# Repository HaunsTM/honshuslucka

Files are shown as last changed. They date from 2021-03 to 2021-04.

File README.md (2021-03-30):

# Chicken house hatch

## Introduction
Chicken house hatch is an example of adapted IoT. It all started as an expressed need of automation for the hatch of a chicken house. In the particular area, roosters weren't allowed to make their morning sounds before 8 A.M. The most peaceful solution was to be able to open/close the hatch remotely via a home automation system, Home Assistant.

This  setup is constituted of

* a PLC (ESP8266/D1 mini with wifi)
* a 12 volt DC / 2 ampere linear actuator
* a 2 relay module
* 2 switch buttons
* a hatch for closing/opening the entrance, constructed as a guillotine

Software

The managing software is developeped as a standard Arduino application and written in C++. Architecturally, it is set up as a state machine. For remote controlling puposes, there is a REST-API as well. State changes are reported as MQTT messages.

## Communication
The actuator can be controlled via either direct switches or remotely via http endpoints.

### Devive info
	example: [link](http://10.0.0.71/info)
	
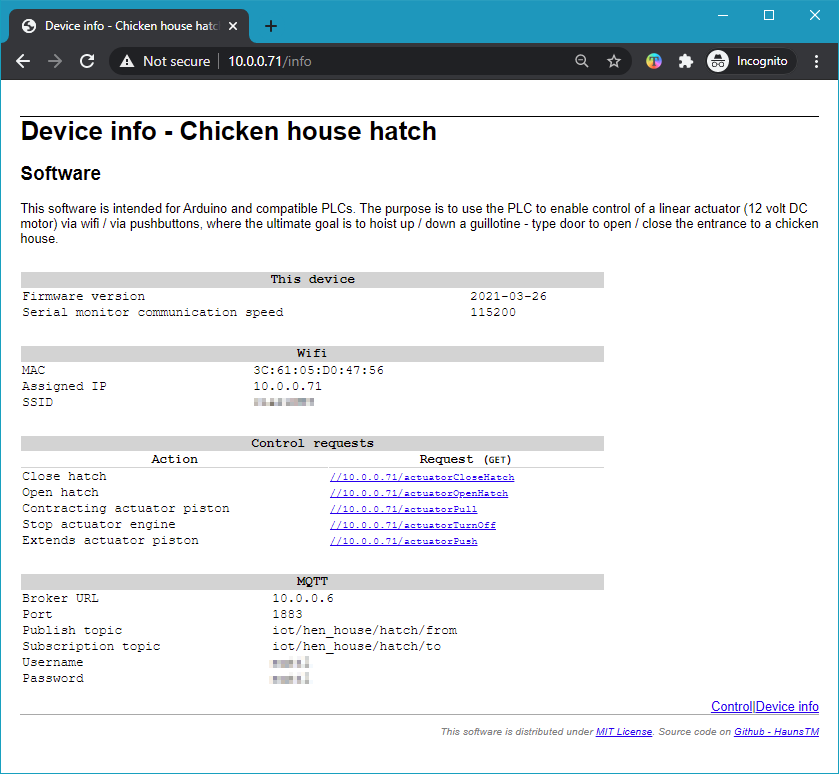
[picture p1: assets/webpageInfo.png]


### Controlling

_server.on("/", [this]() { routeGetControl(); });
<table>
    <thead>
        <tr><td>Action</td><td>Request (GET)</td></tr>
    </thead>
    <tbody>
        <tr><td>Close hatch</td><td>//10.0.0.71/actuatorCloseHatch</td></tr>
        <tr><td>Open hatch</td><td>//10.0.0.71/actuatorOpenHatch</td></tr>
    </tbody>
</table>

<table>
    <thead>
        <tr><td>Action</td><td>Request (GET)</td></tr>
    </thead>
    <tbody>
        <tr><td>Contracting actuator piston</td><td>//10.0.0.71/actuatorPull</td></tr>
        <tr><td>Stop actuator engine</td><td>//10.0.0.71/actuatorTurnOff</td></tr>
        <tr><td>Extends actuator piston</td><td>//10.0.0.71/actuatorPush</td></tr>
    </tbody>
</table>

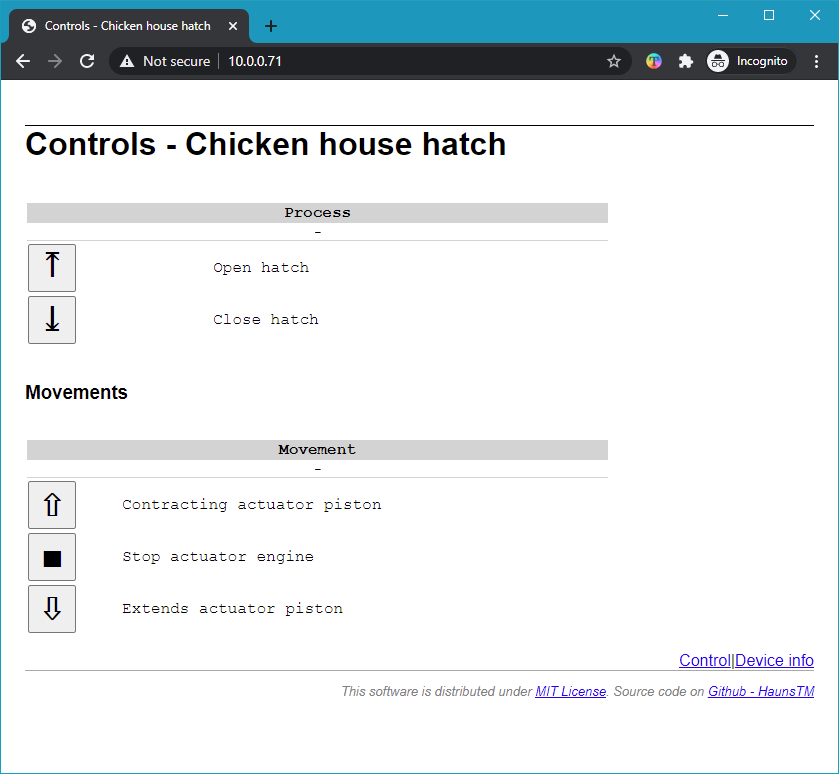
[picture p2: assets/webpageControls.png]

### Reporting
Actions/statuses can be reported to a MQTT broker if such is defined in SettingsData.h.  This file is not in Github for obvious reasons. <i>Example: </i> 
<figure>
<pre>
#ifndef SETTINGS_DATA_H
#define SETTINGS_DATA_H

String SETTINGS_DATA_FIRMWARE_VERSION = "2021-03-29";
int SETTINGS_DATA_SERIAL_MONITOR_BAUD = 115200;

bool ACTUATOR_PULL_WILL_OPEN_HATCH = true;

// WiFi credentials
String CREDENTIALS_JSON_STRING = "["
	"{"
		"\"SSID\": \"&lt;SSID1&gt;\","
		"\"password\": \"&lt;password for wifi>\"},"
	"{"
		"\"SSID\": \"&lt;SSID 2&gt;\","
		"\"password\": \"&lt;password for wifi 2&gt;\"}"
"]";

// Web server
int SETTINGS_DATA_WEB_SERVER_PORT = 80;

// MQTT Broker
String SETTINGS_DATA_MQTT_BROKER_URL = "10.0.0.6";
String SETTINGS_DATA_MQTT_TOPIC_SUBSCRIBE = "iot/hen_house/hatch/to";
String SETTINGS_DATA_MQTT_TOPIC_PUBLISH = "iot/hen_house/hatch/from";
String SETTINGS_DATA_MQTT_USERNAME = "&lt;username for MQTT-broker&gt;";
String SETTINGS_DATA_MQTT_PASSWORD = "&lt;username for MQTT-broker&gt;";
int SETTINGS_DATA_MQTT_PORT = 1883;

#endif
</pre>

  <figcaption><code>SettingsData.h</code></figcaption>
</figure>

# Setup
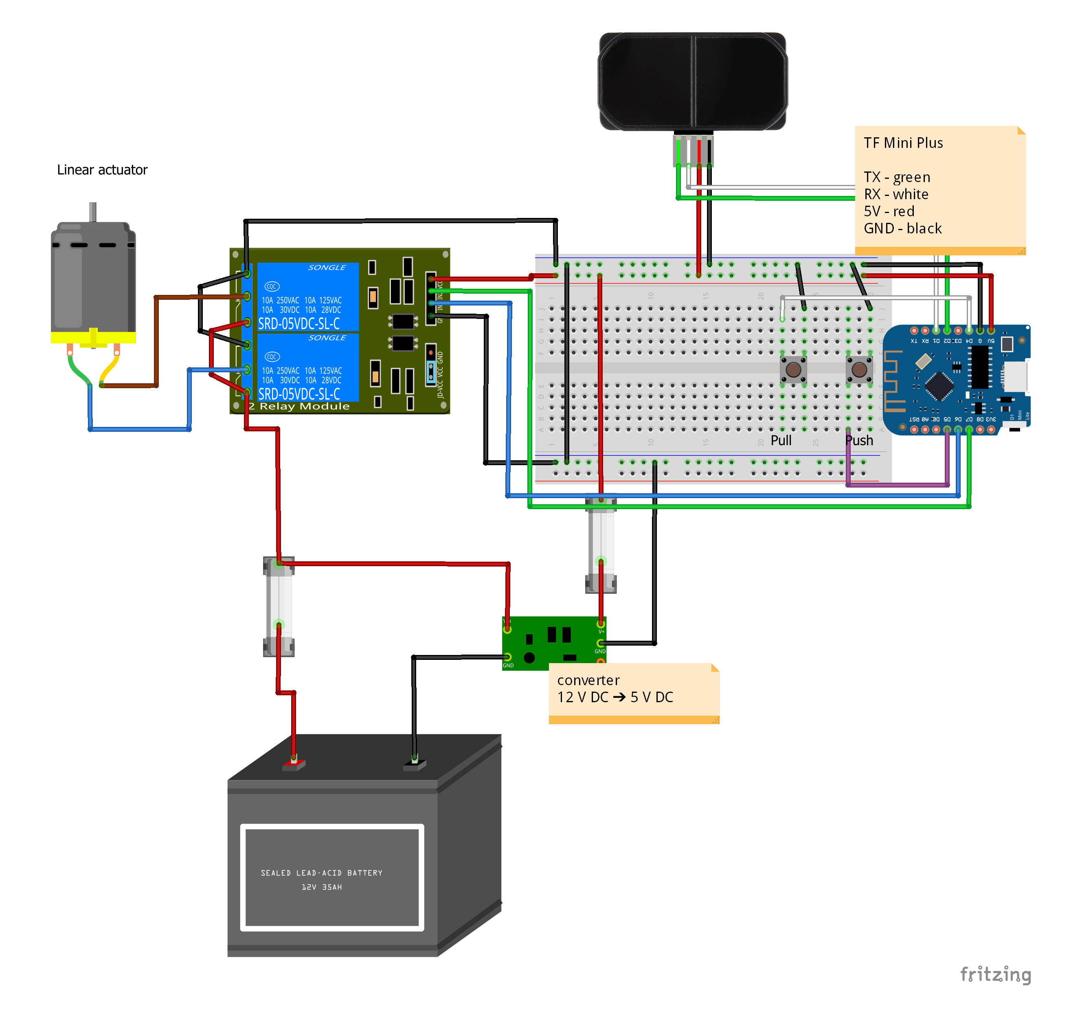
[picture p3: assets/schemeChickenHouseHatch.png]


## Status

Different statuses are indicated with the blue online LED. Different statuses are indicated by different statuses 
<table>
    <thead>
        <tr><td>Action</td><td>Request (GET)</td></tr>
    </thead>
    <tbody>
        <tr><td>error state</td><td>3 short blinks every second</td></tr>
        <tr><td>on http request</td><td>2 short blinks</td></tr>
        <tr><td>on performing action</td><td>1 short blink every second</td></tr>
        <tr><td>stand by</td><td>1 short blink every 5 s</td></tr>
        <tr><td>stand by no wifi</td><td>3 short blinks 5 s</td></tr>
    </tbody>
</table>

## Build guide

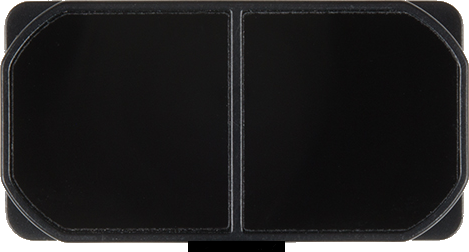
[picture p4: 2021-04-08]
wiringDiagram/tFMiniPlus.png

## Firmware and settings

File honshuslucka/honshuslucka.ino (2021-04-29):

#include <Arduino.h>
#include "Actuator.h"
#include "ActuatorAction.h"
#include "Blinker.h"
#include "DistanceMeter.h"
#include <ESP8266WiFi.h>
#include "HTTPWebServer.h"
#include "HatchRequest.h"
#include "MQTTCommunicator.h"
#include "OnboardLED.h"
#include "Pins.h"
#include <PubSubClient.h>
#include "SettingsData.h"
#include <SoftwareSerial.h>
#include "Switch.h"
#include "SwitchesManager.h"
#include "TextMessageGenerator.h"
#include <TFMPlus.h>  // Include TFMini Plus Library v1.4.1
#include "WifiManager.h"

TFMPlus tfmP;         // Create a TFMini Plus object  
SoftwareSerial mySerial(PIN_D2_GPIO4_SDA, PIN_D1_GPIO5_SCL); //define software serial port name as mySerial and define D5 as RX and D0 as TX
DistanceMeterData currentMeterData;
DistanceMeterData previousMeterData;
DistanceMeter distanceMeter(mySerial, currentMeterData);

OnboardLED onboardLED;
Blinker blinker(onboardLED);

Actuator actuator(PIN_D6_GPIO12_MISO, PIN_D7_GPIO13_MOSI);

Switch actuatorPullButton(PIN_D3_GPIO0_FLASH, true);
Switch actuatorPushButton(PIN_D5_GPIO14_SCLK, true);

TextMessageGenerator tMG(
    SETTINGS_DATA_FIRMWARE_VERSION, SETTINGS_DATA_SERIAL_MONITOR_BAUD,
    SETTINGS_DATA_MQTT_BROKER_URL, SETTINGS_DATA_MQTT_PORT_1883,
    SETTINGS_DATA_MQTT_USERNAME, SETTINGS_DATA_MQTT_PASSWORD);

HatchRequest hatchRequests[2] = { HatchRequest("switch button requested"), HatchRequest("http requested") };

WiFiClient wifiClient;
PubSubClient pubSubClient(wifiClient);
ESP8266WebServer eSP8266WebServer(SETTINGS_DATA_WEB_SERVER_PORT);

void initiateRequestArray() {
    hatchRequests[0].initialize();
    hatchRequests[1].initialize();
}

SwitchesManager switchesManager(hatchRequests[0], actuatorPullButton, actuatorPushButton);

WifiManager wifiManager( tMG, CREDENTIALS_JSON_STRING);

HTTPWebServer webserver(
    hatchRequests[1], eSP8266WebServer,
    tMG, currentMeterData,
    SETTINGS_DATA_MQTT_BROKER_URL,
    SETTINGS_DATA_MQTT_PORT_FOR_PAHO_1884,
    SETTINGS_DATA_MQTT_USERNAME, SETTINGS_DATA_MQTT_PASSWORD,
    SETTINGS_DATA_MQTT_PUBLISHED_TOPIC_ACTUATOR_ACTION,
    SETTINGS_DATA_MQTT_PUBLISHED_TOPIC_LIDAR_DISTANCE_TO_OBJECT_CM, SETTINGS_DATA_MQTT_PUBLISHED_TOPIC_LIDAR_STRENGTH_OR_QUALITY_OF_RETURN_SIGNAL,
    SETTINGS_DATA_MQTT_PUBLISHED_TOPIC_LIDAR_TEMPERATURE_INTERNAL_OF_LIDAR_SENSOR_CHIP_SENSOR);

MQTTCommunicator mQTTC(
    pubSubClient, tMG,
    SETTINGS_DATA_MQTT_BROKER_URL, SETTINGS_DATA_MQTT_PORT_1883,
    SETTINGS_DATA_MQTT_USERNAME, SETTINGS_DATA_MQTT_PASSWORD,
    SETTINGS_DATA_MQTT_PUBLISHED_TOPIC_ACTUATOR_ACTION,
    SETTINGS_DATA_MQTT_PUBLISHED_TOPIC_LIDAR_DISTANCE_TO_OBJECT_CM, SETTINGS_DATA_MQTT_PUBLISHED_TOPIC_LIDAR_STRENGTH_OR_QUALITY_OF_RETURN_SIGNAL,
    SETTINGS_DATA_MQTT_PUBLISHED_TOPIC_LIDAR_TEMPERATURE_INTERNAL_OF_LIDAR_SENSOR_CHIP_SENSOR);

enum class ChickenHatchStates {
    STAND_BY,
    MOVE,
    STOP,
    WAIT_1_S
}; 

ChickenHatchStates state;
HatchRequestAction currentHighestPrioritizedHatchRequestAction;
ActuatorAction currentActuatorActionToPerform;
ActuatorAction previousActuatorAction;
unsigned long hatchMovementStarted;
unsigned long hatchPauseChrono;

void setup() {
    Serial.begin(SETTINGS_DATA_SERIAL_MONITOR_BAUD); // initialize serial monitor with 115200 baud
    delay(20);
    distanceMeter.initialize();
    delay(500);            // And wait for half a second.

    onboardLED.initialize();

    blinker.initialize();
    blinker.start();
     
    actuator.initialize();
    previousActuatorAction = ActuatorAction::TURN_OFF;
    actuatorPullButton.initialize();
    actuatorPushButton.initialize();

    switchesManager.initialize();

    wifiManager.initialize();
    webserver.initialize();
    mQTTC.initialize();

    state = ChickenHatchStates::STAND_BY;

    initiateRequestArray();
}

bool requestsForSameLevel() {
    // this should be determined with LIDARS
    return false;
}

bool requestsForOtherLevel() {

    const bool buttonRequestActionIsNotStop = hatchRequests[0].getAction() != HatchRequestAction::STOP;
    const bool buttonRequestIsNotAcknowledged = !hatchRequests[0].getAcknowledged();

    const bool buttonRequestActionIsNotStopAndIsNotAcknowledged = buttonRequestActionIsNotStop && buttonRequestIsNotAcknowledged;


    const bool httpRequestActionIsNotStop = hatchRequests[1].getAction() != HatchRequestAction::STOP;
    const bool httpRequestIsNotAcknowledged = !hatchRequests[1].getAcknowledged();

    const bool httpRequestActionIsNotStopAndIsNotAcknowledged = httpRequestActionIsNotStop && httpRequestIsNotAcknowledged;

    if (buttonRequestActionIsNotStopAndIsNotAcknowledged || httpRequestActionIsNotStopAndIsNotAcknowledged) {

        return true;
    }

    return false;

}

HatchRequestAction getPrioritizedHatchRequestAction() {

    /*
    if (actionRequests[1].getAction() == ActuatorAction::TURN_OFF) { // turn off, http-request most important
        return actionRequests[1].getAction();
    }*/
    if (!hatchRequests[0].getAcknowledged()) { // 1st important (button request)
        return hatchRequests[0].getAction();
    }
    if (!hatchRequests[1].getAcknowledged()) { // 2nd important (http requeest)
        return hatchRequests[1].getAction();
    }
}

bool stopRequested() {
    // this function exist for safety, any release of real button/html button will generate a stop request which always should be most important

    // we should have lidar logic here as well

    if (!hatchRequests[0].getAcknowledged() && (hatchRequests[0].getAction() == HatchRequestAction::STOP)) { // 1st important (button request)
        return true;
    }

    if (!hatchRequests[1].getAcknowledged() && (hatchRequests[1].getAction() == HatchRequestAction::STOP)) { // 2nd important (http requeest)
        return true;
    }
    return false;
}

bool maxHatchMovementTimeReached() {

    unsigned long currentTimeMs = millis();

    if (currentTimeMs < hatchMovementStarted) {
        // special case - we have rounded max time
        return true;
    }

    const bool maxTimeReached = currentTimeMs > (hatchMovementStarted + MAX_REQUIRED_TIME_TO_PERFORM_A_HATCH_OPEN_PROCESS_MS);
    return maxTimeReached;
};

ActuatorAction acknowledgeAllCurrentHacthRequests() {

    hatchRequests[0].setAcknowledged(true);
    hatchRequests[1].setAcknowledged(true);
}

ActuatorAction hatchAction2ActuatorAction(HatchRequestAction hatchAction) {
    ActuatorAction actuatorAction;

    switch (hatchAction) {
        case HatchRequestAction::UP:
            actuatorAction = ACTUATOR_PULL_WILL_OPEN_HATCH ? ActuatorAction::PULL : ActuatorAction::PUSH;
            break;
        case HatchRequestAction::STOP:
            actuatorAction = ActuatorAction::TURN_OFF;
            break;
        case HatchRequestAction::DOWN:
            actuatorAction = ACTUATOR_PULL_WILL_OPEN_HATCH ? ActuatorAction::PUSH : ActuatorAction::PULL;
            break;
        case HatchRequestAction::CLOSE_HATCH:
            actuatorAction = ACTUATOR_PULL_WILL_OPEN_HATCH ? ActuatorAction::PUSH : ActuatorAction::PULL;
            break;
        case HatchRequestAction::OPEN_HATCH:
            actuatorAction = ACTUATOR_PULL_WILL_OPEN_HATCH ? ActuatorAction::PULL : ActuatorAction::PUSH;
            break;
    }
    return actuatorAction;
}

void performCurrentActuatorAction() {

    switch (currentActuatorActionToPerform) {

        case ActuatorAction::TURN_OFF:
            actuator.turnOFF();
            break;

        case ActuatorAction::PULL:
            actuator.pull();
            break;

        case ActuatorAction::PUSH:
            actuator.push();
            break;
    }
}

void reportChangesInCurrentActuatorAction() {

    if (currentActuatorActionToPerform != previousActuatorAction) {
        mQTTC.reportHen_HouseHatchActuatorAction(currentActuatorActionToPerform);
        previousActuatorAction = currentActuatorActionToPerform;
    }
};

void chickenHatchStateMachine() {

    switch (state)
    {

        case ChickenHatchStates::STAND_BY:

            currentActuatorActionToPerform = ActuatorAction::TURN_OFF;
            
            wifiManager.isConnectedToWifi() ? blinker.setBlinkerSequence(Blinker::BlinkerSequence::STAND_BY) : blinker.setBlinkerSequence(Blinker::BlinkerSequence::STAND_BY_NON_WIFI);

            if (requestsForSameLevel()) {
                state = ChickenHatchStates::STOP;
            }
                      
            else if (requestsForOtherLevel()) {
                currentHighestPrioritizedHatchRequestAction = getPrioritizedHatchRequestAction();
                acknowledgeAllCurrentHacthRequests();

                currentActuatorActionToPerform = hatchAction2ActuatorAction(currentHighestPrioritizedHatchRequestAction);
                
                hatchMovementStarted = millis();
                state = ChickenHatchStates::MOVE;
            }
            break;

        case ChickenHatchStates::MOVE:
            blinker.setBlinkerSequence(Blinker::BlinkerSequence::PERFORMING_MOVE);

            if (stopRequested()) {
                acknowledgeAllCurrentHacthRequests();

                state = ChickenHatchStates::STOP;
            }
            
            if (maxHatchMovementTimeReached()) {
                acknowledgeAllCurrentHacthRequests();

                state = ChickenHatchStates::STOP;
            }

            break;

        case ChickenHatchStates::STOP:

            currentActuatorActionToPerform = ActuatorAction::TURN_OFF;

            state = ChickenHatchStates::WAIT_1_S;

            hatchMovementStarted = 0;
            hatchPauseChrono = millis();

            break;
        
        case ChickenHatchStates::WAIT_1_S:

            if (millis() - hatchPauseChrono > 1000) {
                state = ChickenHatchStates::STAND_BY;
            }

            break;

    }   
}

void reportMoving() {

    if (currentMeterData.distanceToObjectCm != previousMeterData.distanceToObjectCm) {
        mQTTC.reportHen_HouseHatchLidar(currentMeterData);
    }

};

void loop() {
    switchesManager.monitorInteractions();
    wifiManager.monitorWiFi();
    webserver.handleClient();

    chickenHatchStateMachine();

    if (wifiManager.isConnectedToWifi()) {
        if (!mQTTC.isConnectedToMQTTBroker()) {
            mQTTC.connectToMQTTBroker();
        }
        pubSubClient.loop();
    }

    performCurrentActuatorAction();
    reportChangesInCurrentActuatorAction();

    blinker.handleBlinker();

    if (distanceMeter.isConnected()) {
        previousMeterData = currentMeterData;
        distanceMeter.handleDistanceMeter();
        reportMoving();
    }
}

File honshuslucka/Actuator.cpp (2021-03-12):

#include <Arduino.h>
#include "Actuator.h"

Actuator::Actuator(int pinRelay1, int pinRelay2) {
  _pinRelay1 = pinRelay1;
  _pinRelay2 = pinRelay2;
  _initialized = false;
}

void Actuator::initialize() {
    if (!_initialized) {
      pinMode(_pinRelay1, OUTPUT);// set pin as output for relay 1
      pinMode(_pinRelay2, OUTPUT);// set pin as output for relay 2   
      
      // keep the motor off
      turnOFF();

      _initialized = true;
    }
}

void Actuator::push() {
  digitalWrite(_pinRelay1, LOW);// turn relay 1 ON
  digitalWrite(_pinRelay2, HIGH);// turn relay 2 OFF 
}
    
void Actuator::pull() {
  digitalWrite(_pinRelay1, HIGH);// turn relay 1 OFF
  digitalWrite(_pinRelay2, LOW);// turn relay 2 ON 
}

void Actuator::turnOFF() {
  digitalWrite(_pinRelay1, HIGH);// turn relay 1 OFF
  digitalWrite(_pinRelay2, HIGH);// turn relay 2 OFF
}

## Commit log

2021-03-18 Webpage is functional but looks ugly on mobile devices
2021-03-23 Can manage the actuator from web as well!
2021-03-30 Work on documentation
    [scheme.fzz]
2021-04-07 Reporting lidar sensor via mqtt Updated invalid HTTP endpoints as well
2021-04-07 Added http endpoint for fetching lidar sensor data
2021-04-08 Started to add new component TFMini Plus for fritzing
    [scheme.fzz]
2021-04-08 Updated wiring diagram
    [scheme.fzz]
2021-04-08 Changed pin, added Vector.h to be a part of the solution
2021-04-08 Updated pins
    [scheme.fzz]
2021-04-15 Added knockout for binding, updated mqtt topics
    [MQTTCommunicator.cpp, honshuslucka.ino]
2021-04-29 bug correction in controls web page
    [honshuslucka.ino]
